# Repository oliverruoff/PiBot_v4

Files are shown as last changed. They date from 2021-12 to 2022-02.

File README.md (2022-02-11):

# PiBot_v4
A small roboter based on a raspberry pi zero w, using lidar for locating.

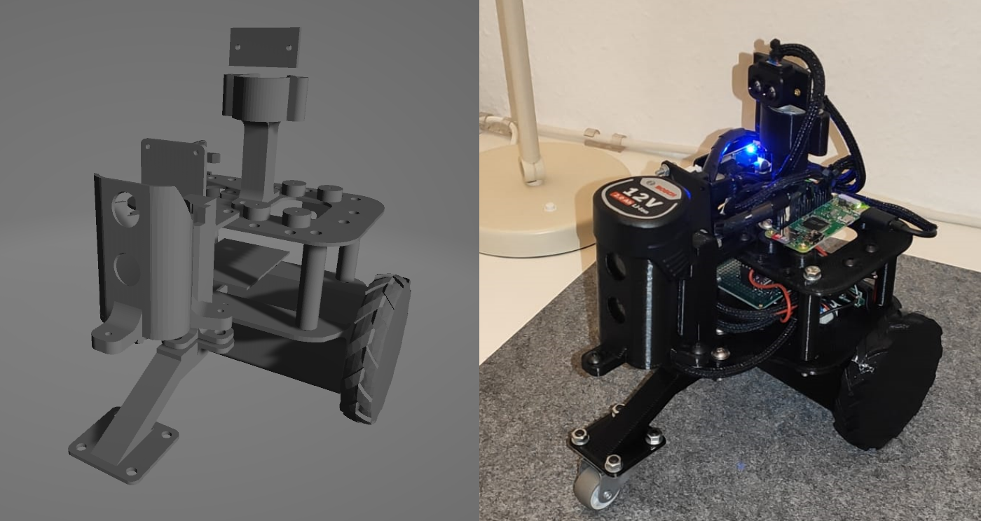
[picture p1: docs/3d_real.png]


## Results

First single mapping with single 360 scan:  
  
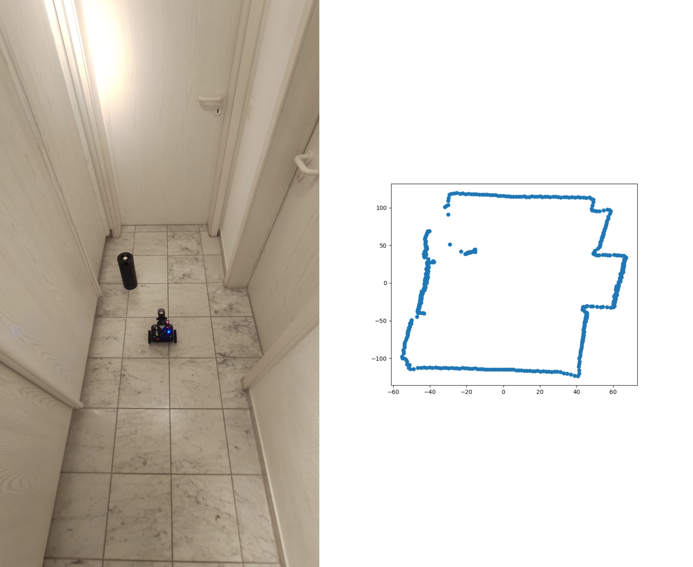
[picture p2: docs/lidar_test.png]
lidar test
  
  
"Manual" mapping results of six double 360 scans stitched together  
(ground truth map grey in the background):    

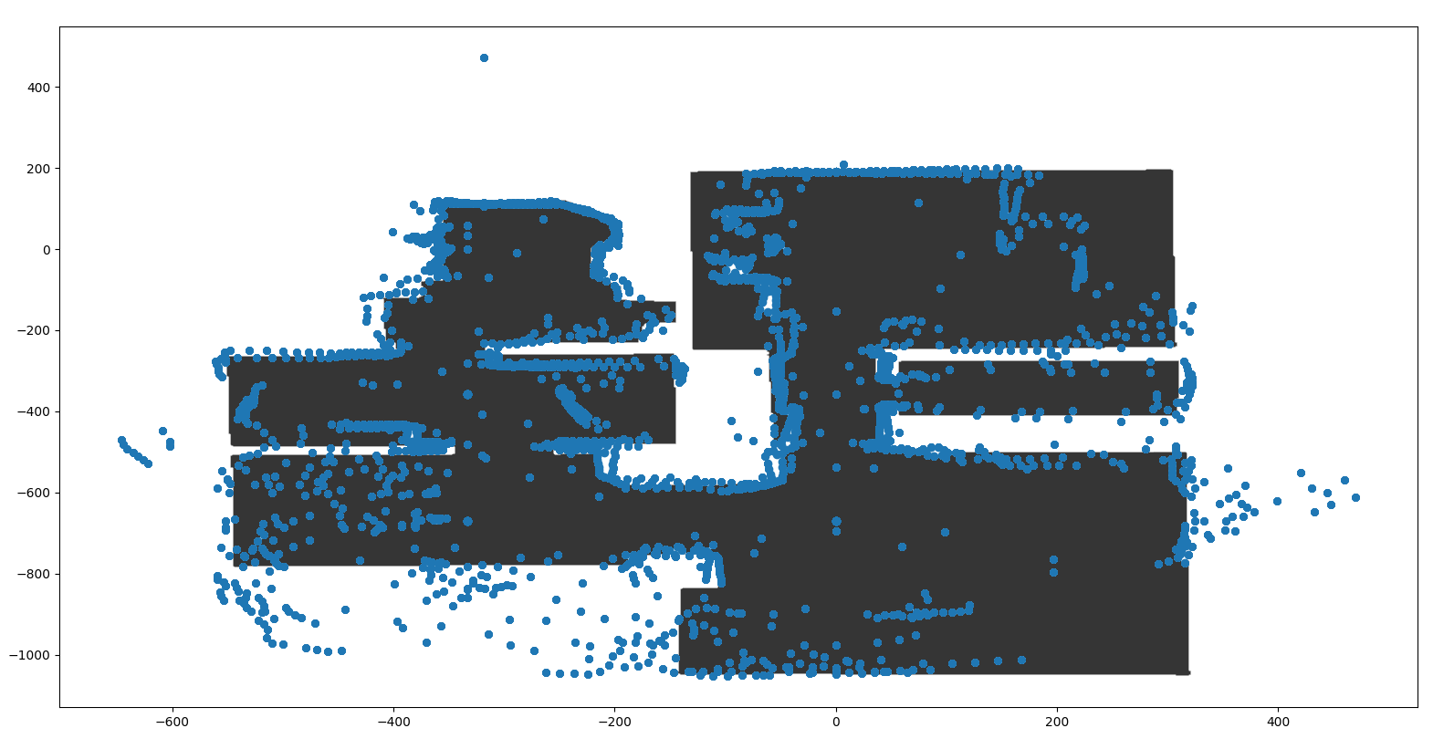
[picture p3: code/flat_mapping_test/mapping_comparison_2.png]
mapping comparison


## Setup

- Install python packages from requirements.txt
- Start pigpio demon on boot
    - `sudo systemctl enable pigpiod`
    - `sudo systemctl start pigpiod`
- Enable serial mode P6 in interacing options (`sudo raspi-config`)

## Printable 3D objects
The robot is designed by myself, the printable 3d objects can be found in the [stls folder](stls/).

## Wiring

Also see [fritzing wiring](docs/PiBot_v4_wiring.fzz).

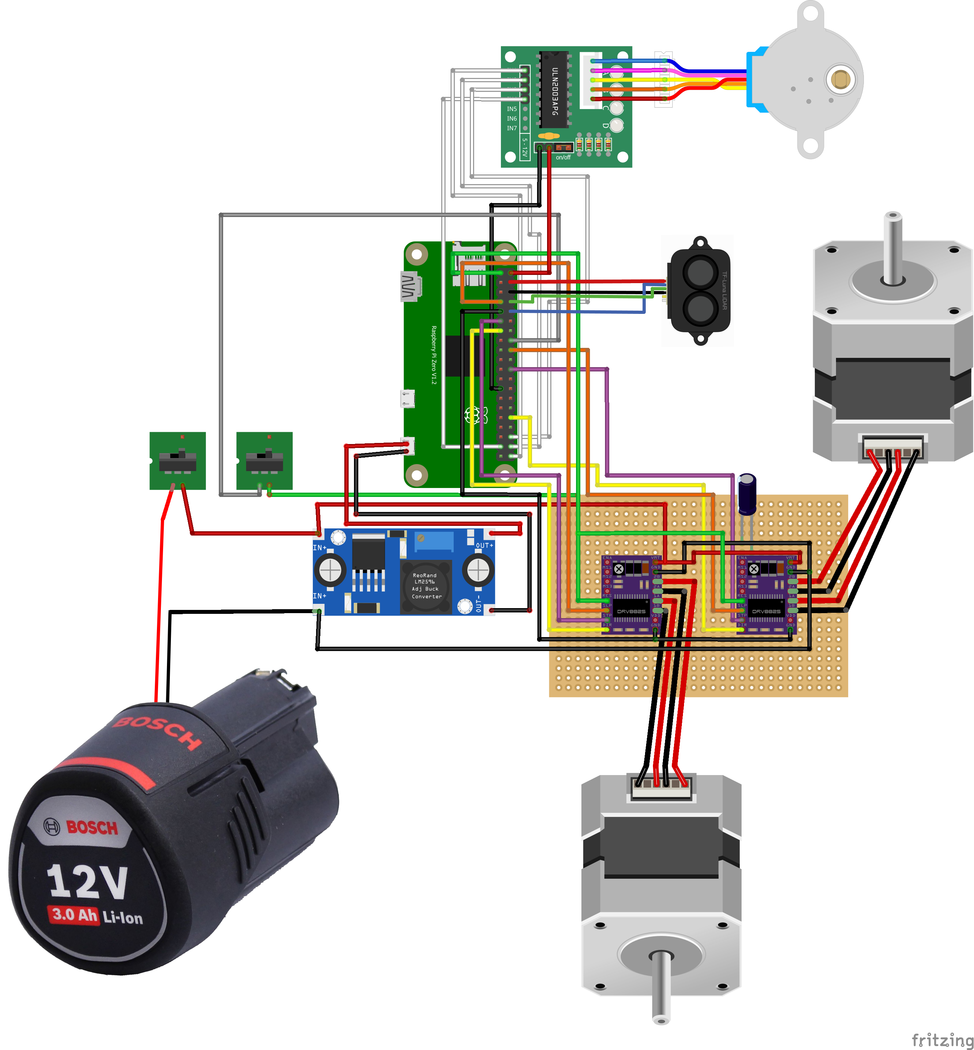
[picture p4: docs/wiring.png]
Breadboard View


## Stepper

To connect the stepper motor to the driver and raspberry, refer to this [youtube video](https://www.youtube.com/watch?v=LUbhPKBL_IU&t=258s).  
Don't miss to adjust the motor driver, so you don't fry your motor. (set current to max. 71% of max. motor current, in this case 1.5A --> driver current max. 1.065A (0.71 x 1.5). You should be fine with around 0.7A). --> For the smaller stepper which moves the lidar on the top, I used 0.5A, since this stepper has an 1A rating.

### Stepper ramping

The robot will slip when accelerating from 0 to 100% speed instantly, so that's why I implemented a ramping function (can be called by setting `ramping` keyword to true in according stepper functions).

The ramping function uses following exponential function:

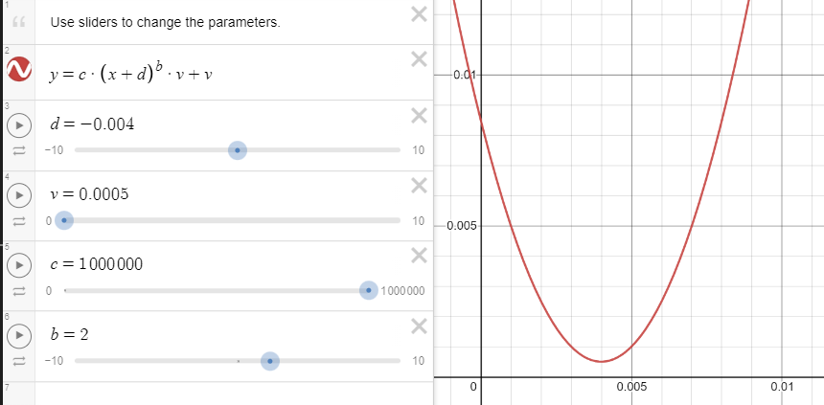
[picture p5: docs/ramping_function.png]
expo function

(using desmos.com) for modeling the function.

## Hardware Used

- Raspberry Pi Zero W
- Stepper Motor + Driver (DRV8825) ( 12V 1.5A) x2
- Stepper Motor + Driver ( 5V ULN2003)
- Power Converter
- TF Luna mini Lidar
- Bosch 12v Battery Pack
- Switches x2
- Voltage meter

### DRV8825 wiring

In order to correctly wire the bigger stepper motors, also see this example wiring:

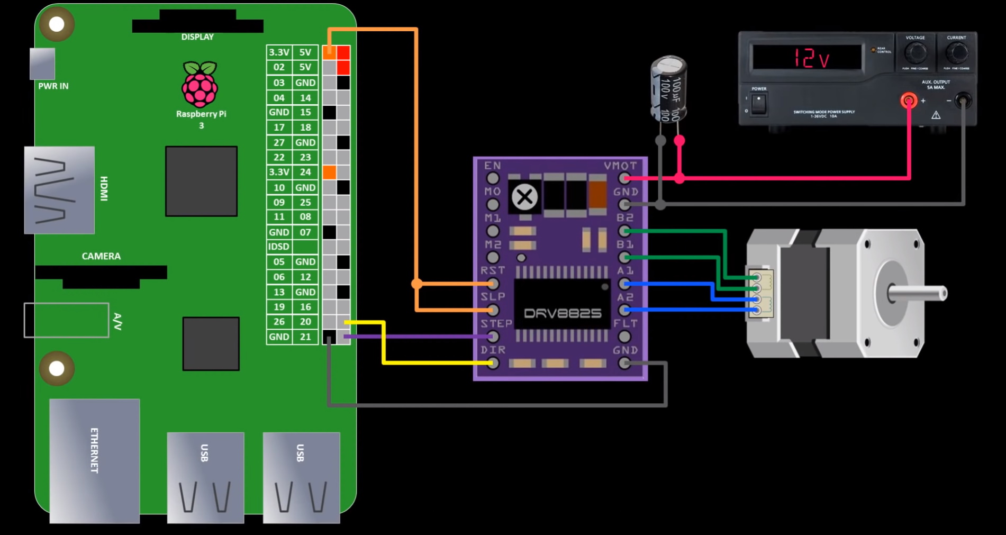
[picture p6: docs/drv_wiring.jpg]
drv wiring


### TF-Luna 

Check the byte codes of the lidar sensor for implementation:
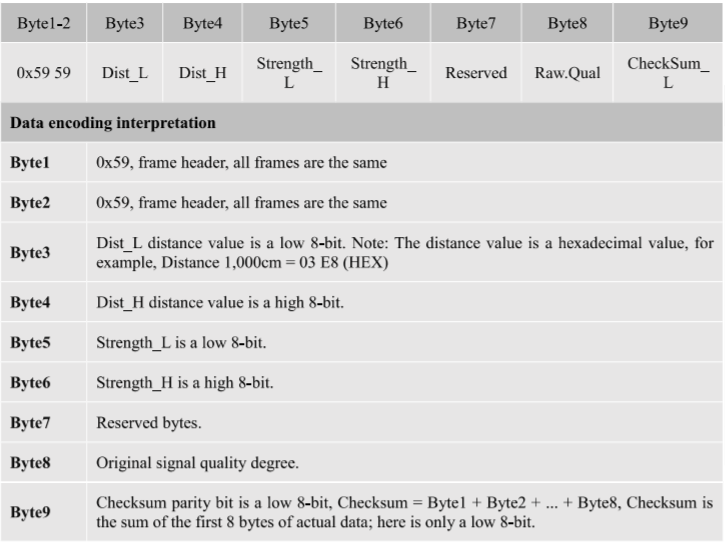
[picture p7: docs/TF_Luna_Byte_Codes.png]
tf-luna byte codes


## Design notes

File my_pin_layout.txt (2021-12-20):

Switch:

GPIO 23

Stepper rechts:

SLP = GPIO 24
STEP = GPIO 25
DIR= GPIO 12

Stepper links:

SLP = GPIO 4
STEP = GPIO 17
DIR = GPIO 27

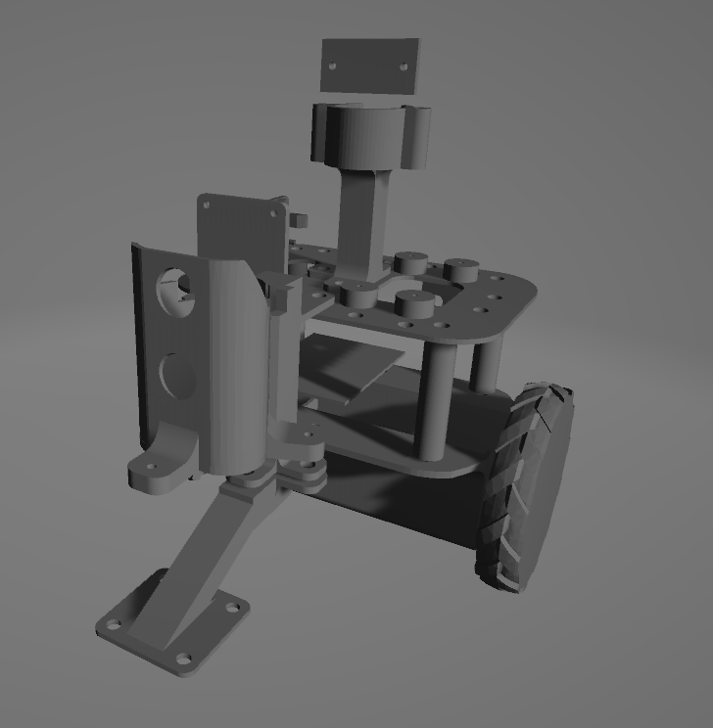
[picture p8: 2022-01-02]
docs/3d_robot.png

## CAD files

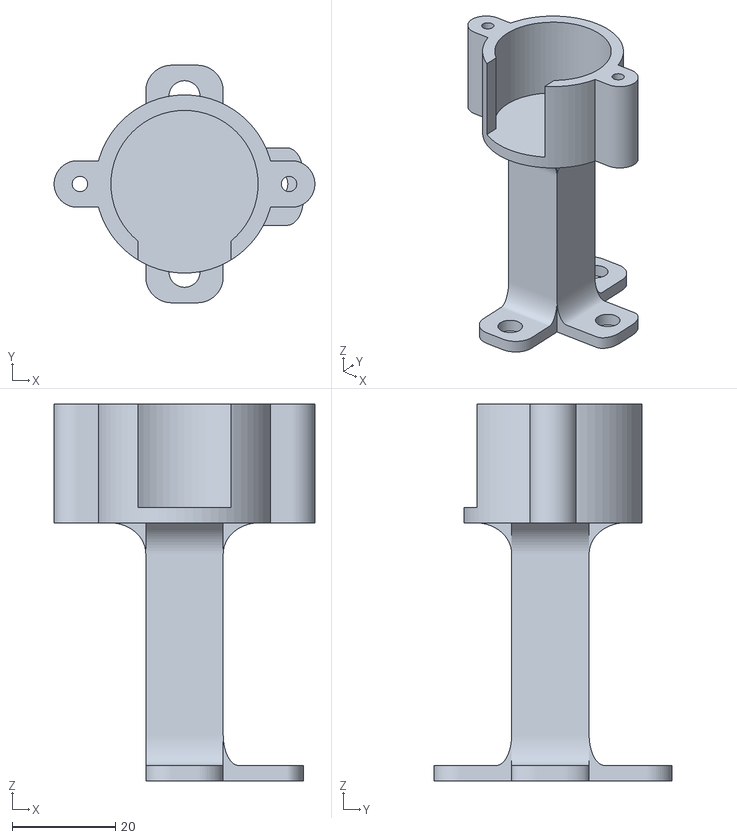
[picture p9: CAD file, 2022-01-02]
stls/PiBot v4_top_stepper_holder.stl
50.5 x 46.0 x 73.0

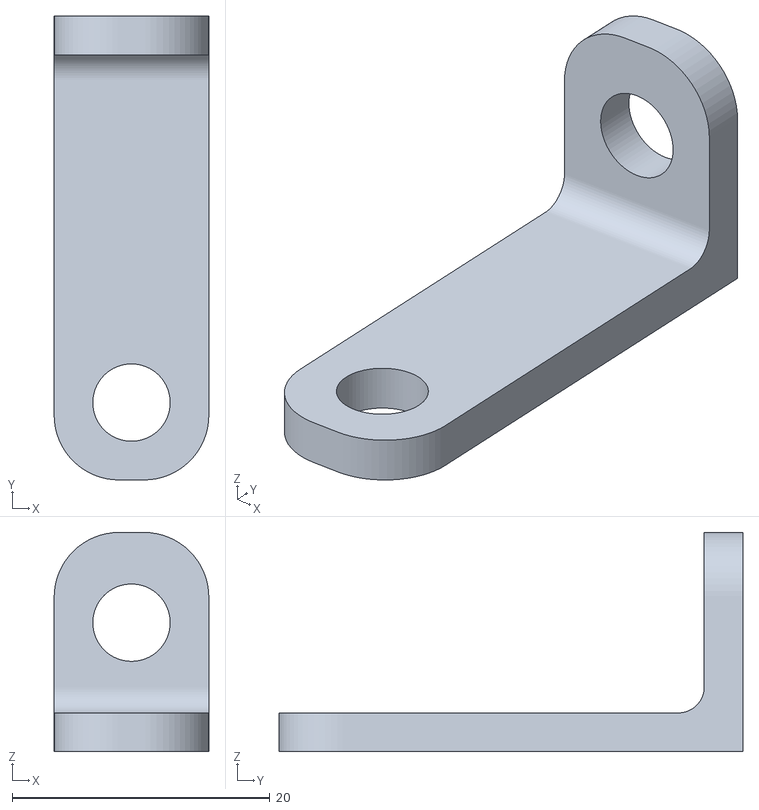
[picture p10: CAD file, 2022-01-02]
stls/PiBot v4_battery_holder_connector.stl
12.0 x 36.0 x 17.0

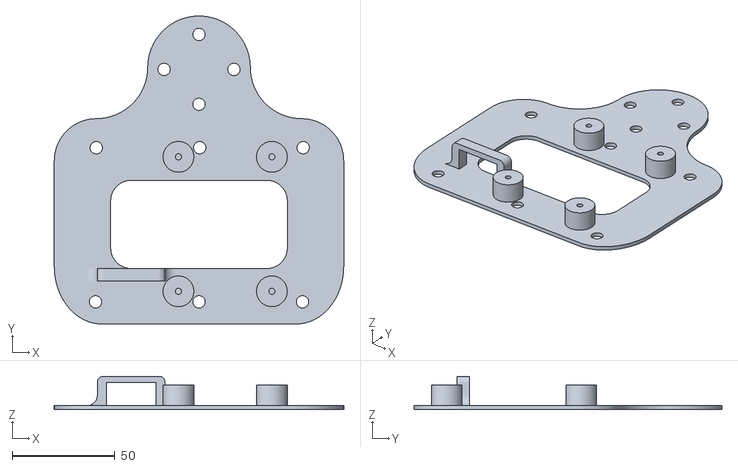
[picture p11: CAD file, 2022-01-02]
stls/PiBot v4_first_level_plate.stl
141.0 x 150.0 x 16.3

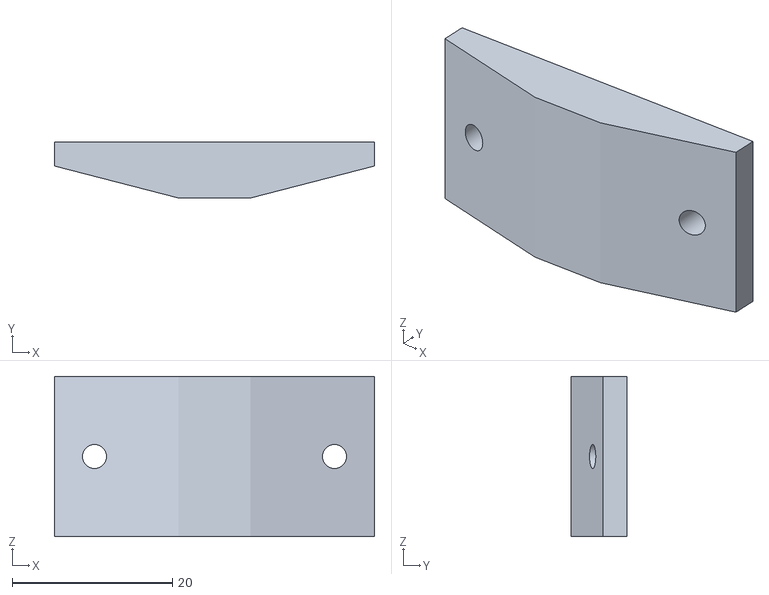
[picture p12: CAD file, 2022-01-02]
stls/PiBot v4_tf_luna_holder.stl
40.0 x 7.00 x 20.0

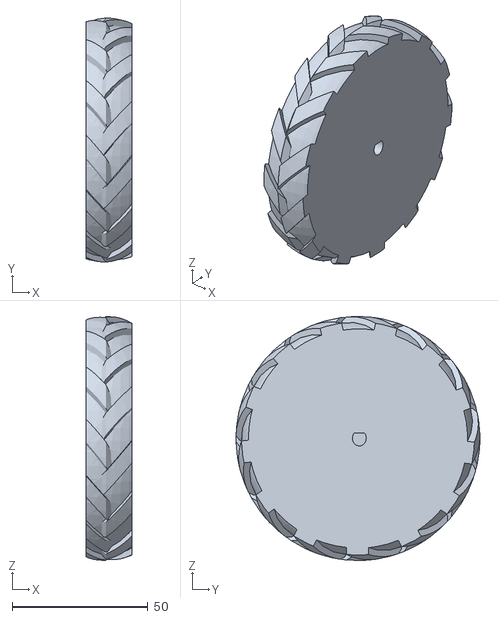
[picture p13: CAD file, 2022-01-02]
stls/PiBot v4_wheel.stl
17.0 x 90.0 x 90.0

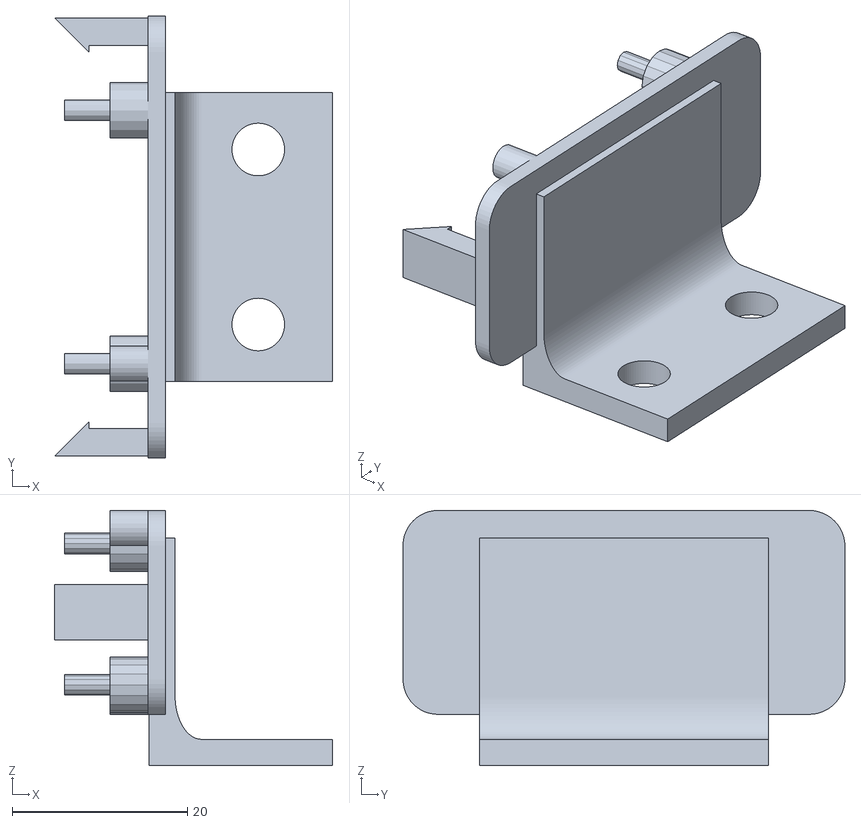
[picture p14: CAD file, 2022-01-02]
stls/PiBot v4_power_converter_holder.stl
31.8 x 50.5 x 29.1

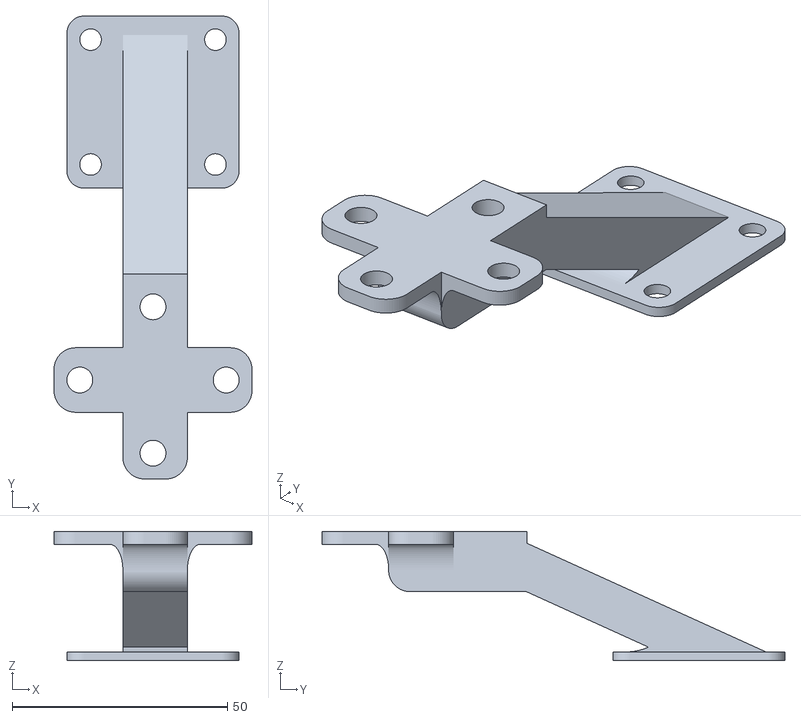
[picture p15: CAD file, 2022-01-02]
stls/PiBot v4_front_wheel_holder.stl
46.0 x 107.6 x 30.0

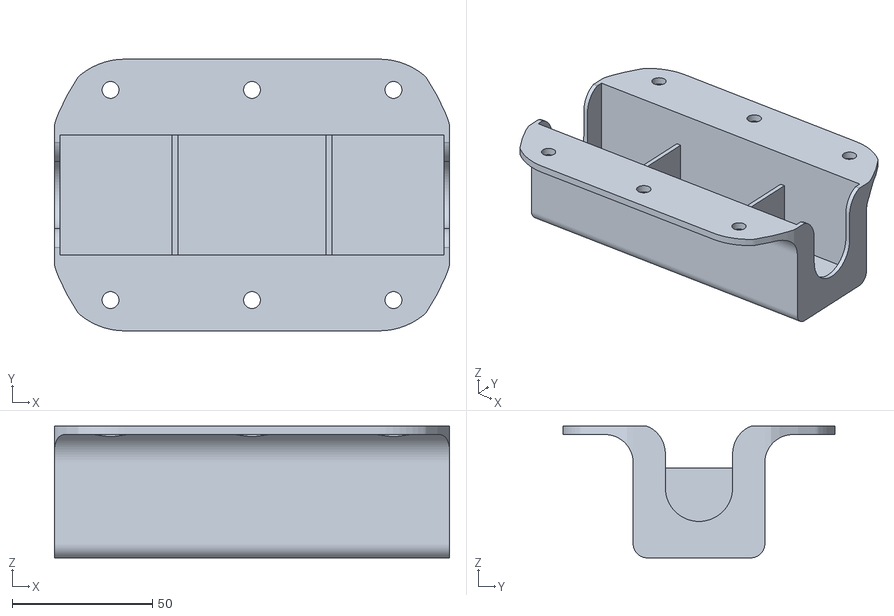
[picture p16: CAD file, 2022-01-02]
stls/PiBot v4_base_stepper_plate.stl
141.0 x 97.0 x 47.0

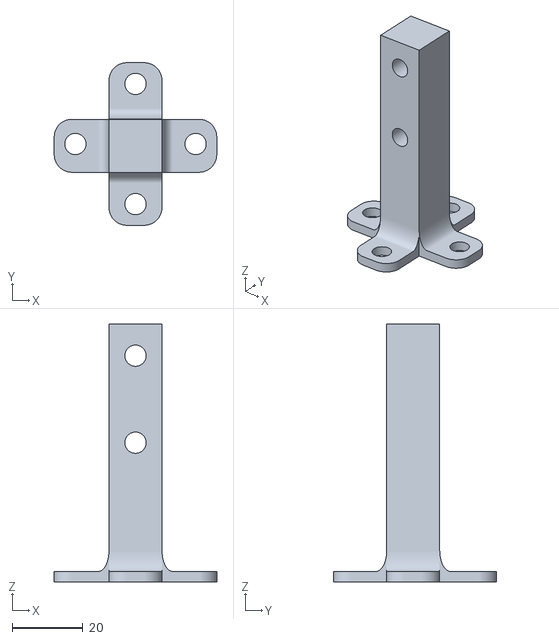
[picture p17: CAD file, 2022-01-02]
stls/PiBot v4_battery_holder.stl
46.0 x 46.0 x 73.0

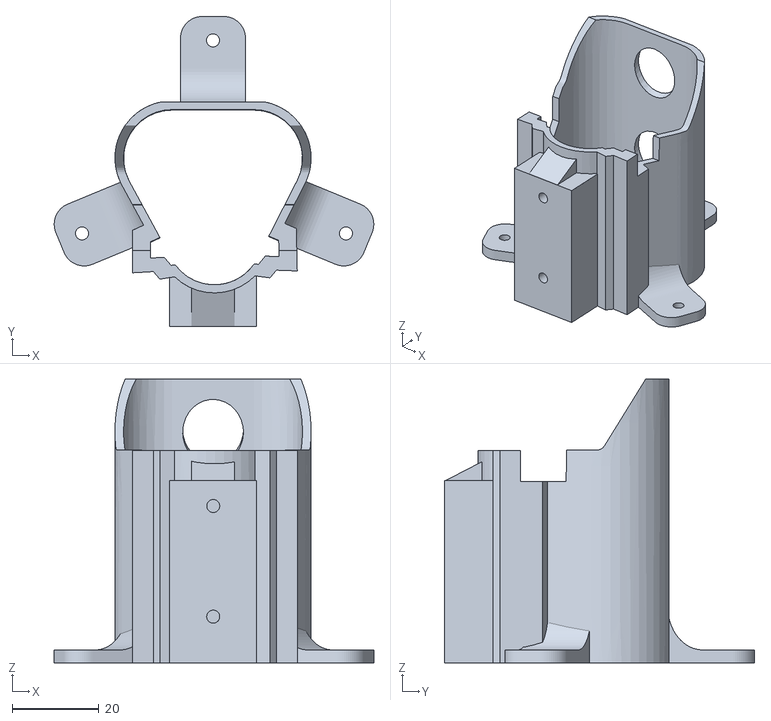
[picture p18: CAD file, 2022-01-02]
stls/PiBot v4_battery_case_top.stl
73.7 x 71.5 x 65.4

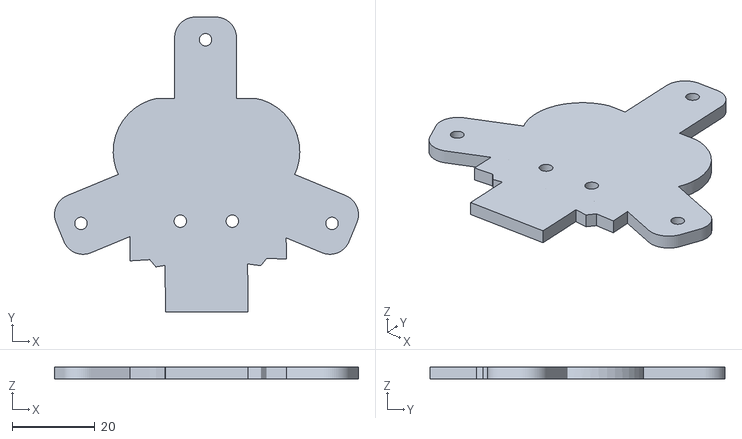
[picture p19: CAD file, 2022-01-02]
stls/PiBot v4_battery_case_bottom.stl
73.7 x 71.5 x 3.00

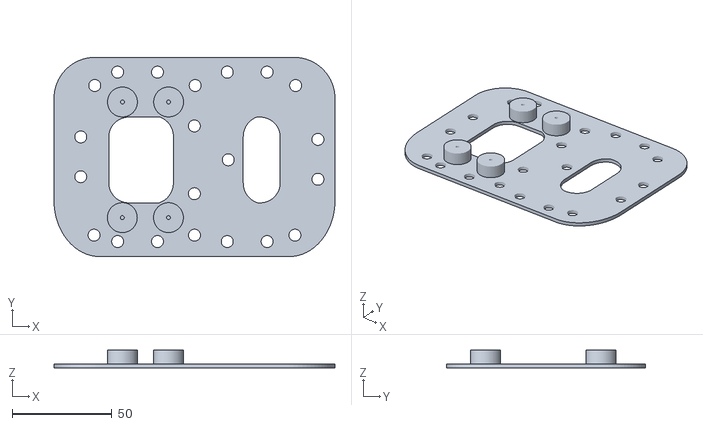
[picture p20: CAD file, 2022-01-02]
stls/PiBot v4_second_level_plate.stl
141.0 x 100.0 x 9.00

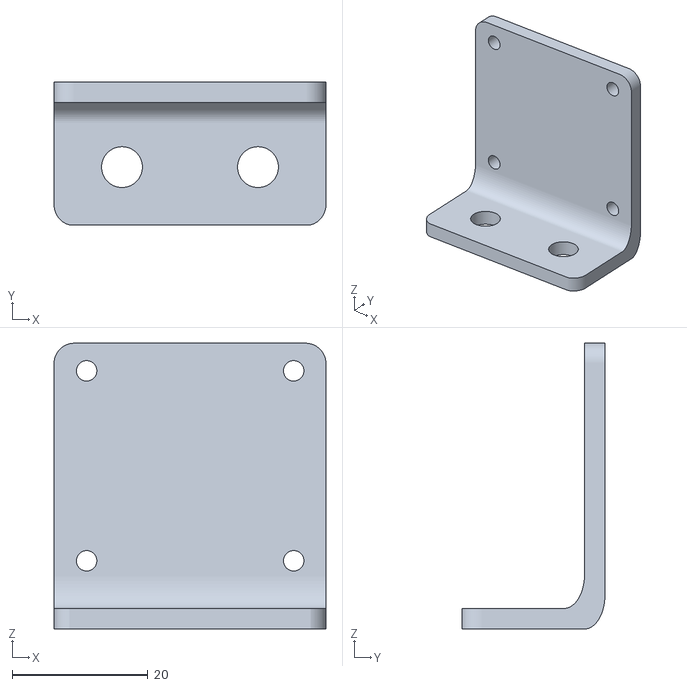
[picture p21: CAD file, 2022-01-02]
stls/PiBot v4_ULN2003_stepper_driver_holder.stl
40.0 x 21.0 x 42.0

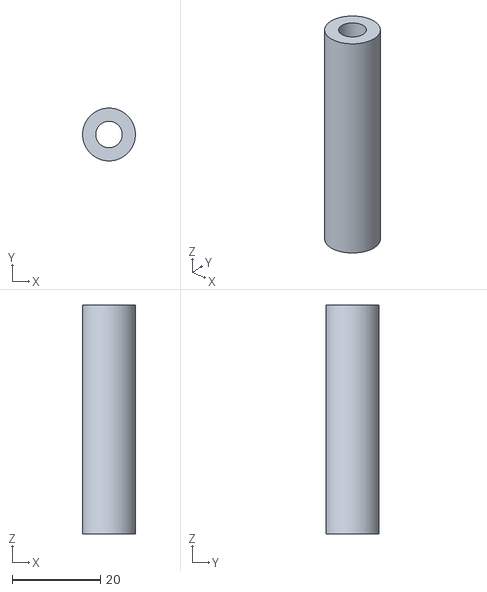
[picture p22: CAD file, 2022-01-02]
stls/PiBot v4_connectors.stl
12.0 x 12.0 x 52.0

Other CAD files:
stls/PiBot v4_switch_holder.stl

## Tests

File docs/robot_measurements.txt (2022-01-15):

Dro = 21,2cm
Uro = 66,6cm
Dre = 9,2
Ure = 28,9

Eine Umdrehung:
66,6 / 28,9 == 2,3
2,3 * 360° == 828°

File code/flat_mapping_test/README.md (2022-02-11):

# Flat Mapping Test

## Description

In this test I'm trying to map my flat by doing 360 scans with the robot on  
specified points.  
Therefore, I manually put the robot exactly to on the points and start a 360 scan  
by hand. The points are precisely measured and their offsets will be used to   
translate the resulting scanned coordinates.  
After postprocessing (translating) the scanned points and stitching them together,  hopefully a rough point cloud describing the flat should result.  

## Measurement points

>Note: The robot is facing the bottom of the map

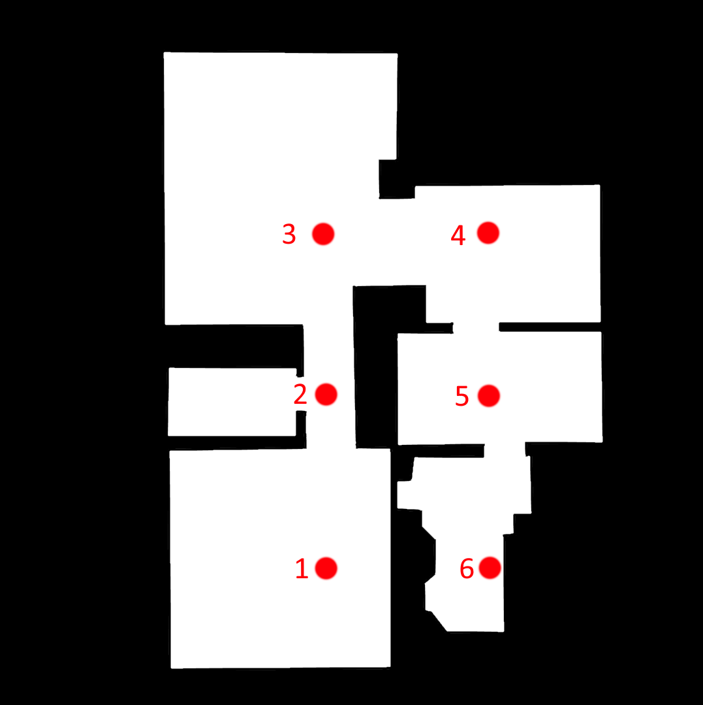
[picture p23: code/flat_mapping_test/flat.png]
flat with points


1.      (0, 0)  
1.      (0, -358)       // +0, -358
1.      (0, -671)       // +0, -313
1.      (-333, -671)    // -333, +0
1.      (-333, -358)    // +0, +313
1.      (-333, 0)       // +0, +358

## Results

Here the results of the approaches are listed.

### Manual movement approach

Comparison of the created point cloud map and the ground truth map:  
  
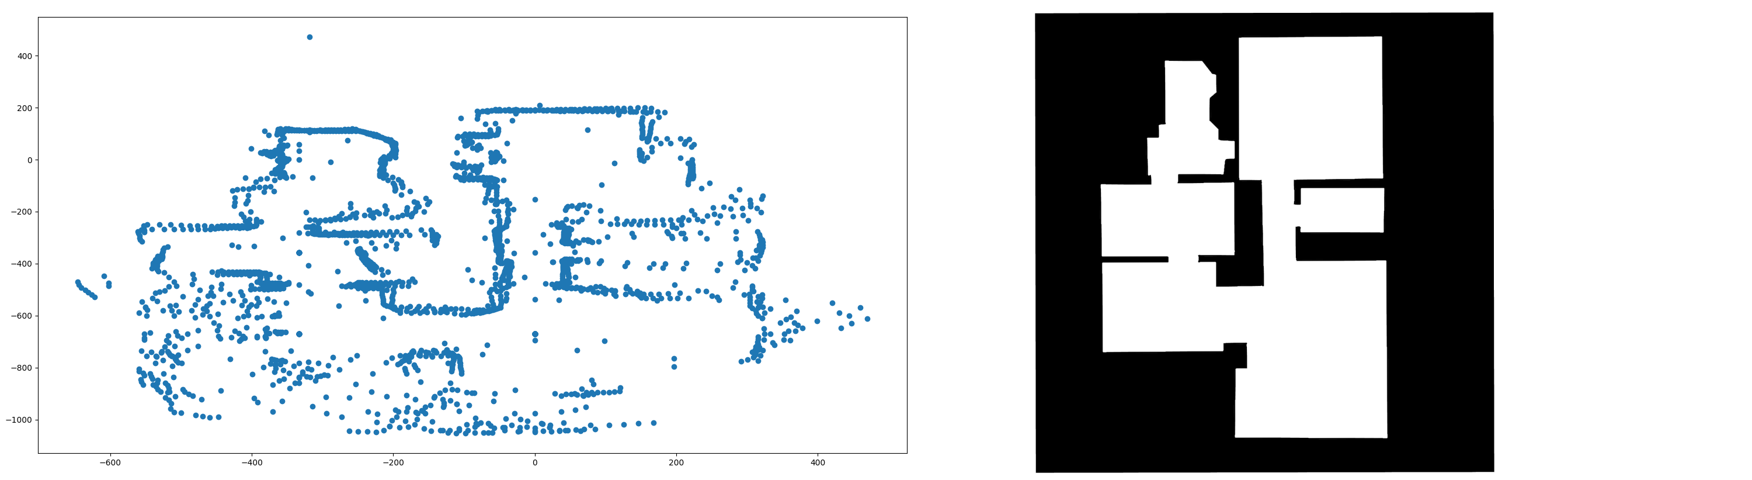
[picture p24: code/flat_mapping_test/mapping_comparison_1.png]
mapping comparison 1
  
  
Comparison of created point cloud map and ground truth map with scaling aligned:  
  
mapping comparison 2

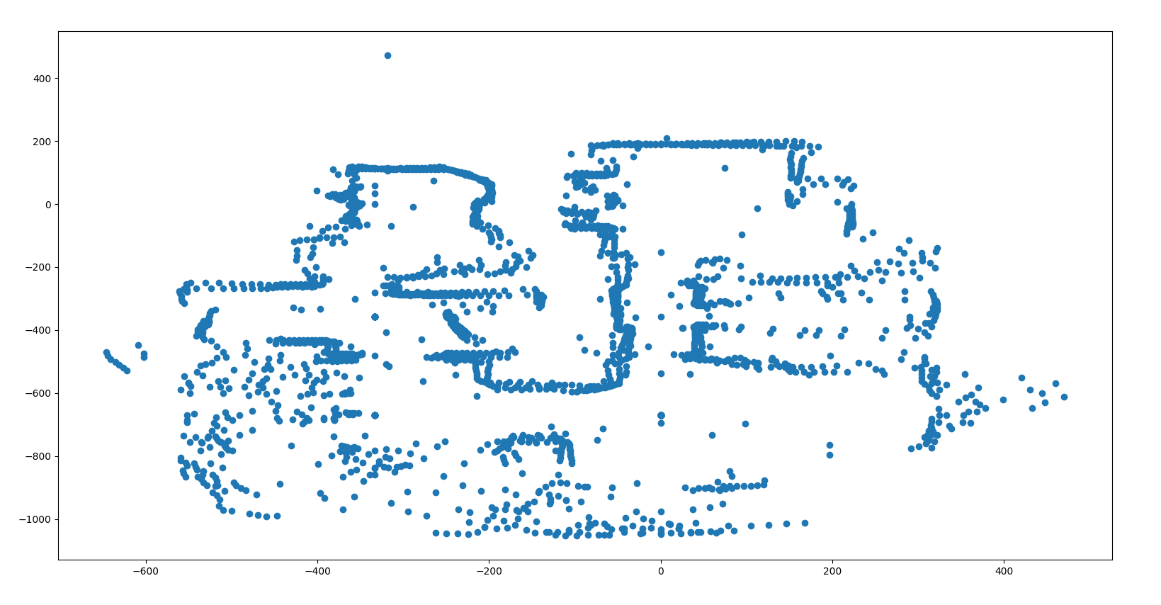
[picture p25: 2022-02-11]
code/flat_mapping_test/mapped_flat_first_attempt.png

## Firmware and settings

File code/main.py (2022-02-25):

from multiprocessing import Process

from actuators import stepper
from sensors import tfluna
from routines import test_all, recorder
from lidar import lidar
from combination import robot
from slam import slam

import RPi.GPIO as GPIO

####################################
# Initializing sensors, motors, etc.
####################################

left_stepper = stepper.stepper(
    DIR=27, STEP=17, SLP=4, steps_per_revolution=200, stepper_delay_seconds=0.0005, gpio_mode=GPIO.BCM)

right_stepper = stepper.stepper(
    DIR=12, STEP=25, SLP=24, steps_per_revolution=200, stepper_delay_seconds=0.0005, gpio_mode=GPIO.BCM)

top_stepper = stepper.stepper(
    DIR=6, STEP=26, SLP=13, RST=19, steps_per_revolution=200, stepper_delay_seconds=0.005, gpio_mode=GPIO.BCM)

tfluna = tfluna.TFLuna()
slam_ = slam.Slam()

robo = robot.Robot(left_stepper, right_stepper, top_stepper, tfluna)

while True:
    inp = input("Input: "). split(" ")
    a = inp[0]
    if a == "1":
        top_stepper.make_one_step()
    elif a == "2":
        # toggle top_stepper direction
        top_stepper.set_direction_clockwise(
            not top_stepper.is_direction_clockwise())
    elif a == "3":
        # drive top_stepper certain angle
        top_stepper.turn_stepper_angle(
            int(inp[1]), asynch=False, ramping=False)
    elif a == "4":
        # drive robot certain distance in cm
        robo.drive_cm(int(inp[1]), bool(inp[2]))
    elif a == "5":
        # turn robot certain angle in degree
        robo.turn_degree(int(inp[1]), bool(inp[2]))
    elif a == "6":
        recorder.record(left_stepper, right_stepper)
    elif a == "7":
        robo.start()
    elif a == "8":
        print(tfluna.read_tfluna_data())
    elif a == "9":
        top_stepper.deactivate_stepper()
        left_stepper.deactivate_stepper()
        right_stepper.deactivate_stepper()
    elif a == "10":
        cloud_1 = robo.lidar.scan_angle_with_stepper_position_reset(360)
        robo.drive_cm(50, forward=True)
        cloud_2 = robo.lidar.scan_angle_with_stepper_position_reset(360)
        moved_cloud = slam_.find_cloud_translation_and_rotation(cloud_1, cloud_2)[
            :-1]
        print(moved_cloud)
        print(moved_cloud[-1])
    elif a == "11":
        cloud_1 = robo.lidar.scan_angle_with_stepper_position_reset(360)
        cloud_2 = slam_.rotate_cloud(cloud_1, 90)
        print("____________________________________")
        print([(i[0], i[1]) for i in cloud_1])
        print("____________________________________")
        print(cloud_2)
    elif a == "12":
        cloud_1 = robo.lidar.scan_angle_with_stepper_position_reset(360)
        robo.drive_cm(50, forward=True)
        cloud_2 = robo.lidar.scan_angle_with_stepper_position_reset(360)
        cloud_3 = slam_.translate_cloud(cloud_2, 0, 50)
        print('Score 1:', slam_.score_2d_clouds(cloud_1, cloud_2))
        print('Score 2:', slam_.score_2d_clouds(cloud_1, cloud_3))
        print("____________________________________")
        print([(i[0], i[1]) for i in cloud_1])
        print("____________________________________")
        print([(i[0], i[1]) for i in cloud_2])
        print("____________________________________")
        print(cloud_3)
    else:
        print("Command not recognized!")

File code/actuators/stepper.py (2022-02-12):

from time import sleep
import threading

import RPi.GPIO as GPIO
import pigpio

CW = 1     # Clockwise Rotation
CCW = 0    # Counterclockwise Rotation


class stepper:
    """This class is for handling the DRV8825 motor driver. E.g. to operate
        common bigger stepper motors.
        """

    def __init__(self, DIR, STEP, SLP, steps_per_revolution, RST=None, stepper_delay_seconds=.005, gpio_mode=GPIO.BCM):
        self.DIR = DIR
        self.STEP = STEP
        self.RST = RST
        # If set to Low, there is no holding torque on the motor
        self.SLP = SLP
        # Steps per Revolution (360 / 1.8) (1,8° per step (oruoff))
        self.steps_per_revolution = steps_per_revolution

        self.stepper_delay_seconds = stepper_delay_seconds
        self.gpio_mode = gpio_mode

        self.pi = pigpio.pi()

        self.direction = CW

        GPIO.setmode(gpio_mode)

        if RST is not None:
            GPIO.setup(self.RST, GPIO.OUT)
            GPIO.output(self.RST, GPIO.HIGH)

        GPIO.setup(self.DIR, GPIO.OUT)
        GPIO.setup(self.STEP, GPIO.OUT)
        GPIO.setup(self.SLP, GPIO.OUT)

        GPIO.output(DIR, CW)

    def set_stepper_delay(self, stepper_delay_seconds):
        """Sets the delay in seconds for the driver to wait between steps.

        Args:
            stepper_delay_seconds (float): Delay in seconds to wait between steps.
        """
        self.stepper_delay_seconds = stepper_delay_seconds

    def activate_stepper(self):
        """Activates the stepper, which also will put holding torque on the stepper.
        This is required in order to move the stepper.
        """
        GPIO.output(self.SLP, GPIO.HIGH)

    def deactivate_stepper(self):
        """Deactivates the stepper and also releases holding torque on the stepper.
        In a deactivated state, the stepper will not be able to move.
        """
        GPIO.output(self.SLP, GPIO.LOW)

    def run_continuously(self, dutycycle=128, frequency=320):
        """Activated, the stepper will continuously run with the desired frequency.
        The dutycycle describes the distribution of high low states, where 128 is 50% / 50% high / low.

        Args:
            dutycycle (int, optional): Describes high / low ratio. 128 is 50%/50%. Defaults to 128.
            frequency (int, optional): Describes the frequency of the stepper's high / low states. Defaults to 320.
        """
        self.activate_stepper()
        self.pi.set_PWM_dutycycle(self.STEP, dutycycle)
        self.pi.set_PWM_frequency(self.STEP, frequency)

    def stop_continuous(self):
        """Stops the continuous turning of the stepper. Also deactivates it, thus
        releasing holding torque.
        """
        self.deactivate_stepper()
        self.pi.set_PWM_dutycycle(self.STEP, 0)

    def set_direction_clockwise(self, clockwise=True):
        """Sets the spinning direction of the stepper motor to clockwise or
        counterclockwise.

        Args:
            clockwise (bool, optional): Spinning direction. Defaults to True.
        """
        self.direction = CW if clockwise else CCW
        GPIO.output(self.DIR, self.direction)

    def is_direction_clockwise(self):
        """Returns True if the current direction set is clockwise, else False.

        Returns:
            bool: True if clockwise, else False.
        """
        return bool(self.direction)

    def turn_stepper_angle(self, degree, asynch, ramping=False):
        """Turns the stepper for a precise angle. Can be called
        either synchronous or asynchronously.

        Args:
            degree (int): The angle in degree, on how much the stepper will
            rotate.
            asynch (bool): Flag wheather this function (and therefore the motor), will turn
            synchronously or asynchronously.
        """
        if (asynch):
            thread = threading.Thread(
                target=self._turn_stepper, args=([degree, ramping]), kwargs={})
            thread.start()
        else:
            self._turn_stepper(degree, ramping)

    def _ramping_function(self, current_step, all_steps):
        """Uses a defined exponential function to output the y value, which can be used
        as delay for the stepper

        Args:
            current_step (int): The current step number (iteratively increased)
            all_steps (int): The number of all steps for the current movement.

        Returns:
            float: The resulting y value, which can be used as stepper delay in seconds.
        """
        X_AXIS_SHIFT = -0.004
        GRAPH_WIDTH = abs(2*X_AXIS_SHIFT)
        EXPONENT = 2
        PARABOLA_SHARPNESS = 1000000
        x = GRAPH_WIDTH/all_steps*current_step
        y = PARABOLA_SHARPNESS*pow(x+X_AXIS_SHIFT, EXPONENT) * \
            self.stepper_delay_seconds + self.stepper_delay_seconds
        return y

    def _turn_stepper(self, degree, ramping=False):
        """This function is for turning the stepper for a precise angle.
        This function should be called with the `turn_stepper_angle` function,
        defining whether the function should run synchronously or asynchronously.

        Args:
            degree (int): The angle in degree, on how much the stepper will rotate.
            ramping (bool): Defines wheather the stepper should ramp up and down its movement.
        """
        self.activate_stepper()
        steps = int(self.steps_per_revolution/360*degree)
        for i in range(steps):
            if ramping:
                delay = self._ramping_function(i, steps)
            else:
                delay = self.stepper_delay_seconds
            GPIO.output(self.STEP, GPIO.HIGH)
            sleep(delay)
            GPIO.output(self.STEP, GPIO.LOW)
            sleep(delay)

    def make_one_step(self):
        """Makes exactly one full step.
        """
        self.activate_stepper()
        GPIO.output(self.STEP, GPIO.HIGH)
        sleep(self.stepper_delay_seconds)
        GPIO.output(self.STEP, GPIO.LOW)
        sleep(self.stepper_delay_seconds)

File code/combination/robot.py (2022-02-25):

from lidar import lidar
import time


class Robot:

    def __init__(self, left_stepper, right_stepper, top_stepper, tfluna):
        self.left_stepper = left_stepper
        self.right_stepper = right_stepper
        self.top_stepper = top_stepper
        self.tfluna = tfluna

        self.position_X = 0
        self.position_Y = 0
        self.heading = 0

        self.TYRE_CIRCUMFERENCE_CM = 28.9              # manually determined
        self.ROBOT_CIRCUMFERENCE_CM = 60.3             # manually determined
        self.TURNING_ERROR_MULTIPLIER = 1.083          # manually determined

        self.lidar = lidar.Lidar(top_stepper=top_stepper, tfluna=tfluna)

    def drive_cm(self, cm, forward, ramping=True):
        if not forward:
            self.left_stepper.set_direction_clockwise(False)
            self.right_stepper.set_direction_clockwise(True)
        else:
            self.left_stepper.set_direction_clockwise(True)
            self.right_stepper.set_direction_clockwise(False)
        desired_angle = (cm / self.TYRE_CIRCUMFERENCE_CM) * \
            360 * self.TURNING_ERROR_MULTIPLIER
        self.left_stepper.turn_stepper_angle(
            desired_angle, True, ramping)
        self.right_stepper.turn_stepper_angle(
            desired_angle, False, ramping)

    def turn_degree(self, degree, clockwise, ramping=True):
        if clockwise:
            self.left_stepper.set_direction_clockwise(False)
            self.right_stepper.set_direction_clockwise(False)
        else:
            self.left_stepper.set_direction_clockwise(True)
            self.right_stepper.set_direction_clockwise(True)

        desired_angle = (self.ROBOT_CIRCUMFERENCE_CM /
                         self.TYRE_CIRCUMFERENCE_CM) * degree * self.TURNING_ERROR_MULTIPLIER
        self.left_stepper.turn_stepper_angle(
            desired_angle, True, ramping)
        self.right_stepper.turn_stepper_angle(
            desired_angle, False, ramping)
        self.heading = (self.heading +
                        degree) % 360 if clockwise else (self.heading - degree) % -360

    def max_distance_routine(self):
        while True:
            env = lidar.scan_360(self.top_stepper, self.tfluna)
            max_dist = 0
            max_angle = 0
            for i in env:
                if i[2] > 800:
                    continue
                if i[2] > max_dist:
                    max_dist = i[2]
                    max_angle = i[3]
            dist_cm = max_dist
            # dist_cm = self.tfluna.read_distance() * 100
            print("Dist:", dist_cm, "at angle:", max_angle)
            if dist_cm > 40:
                self.turn_degree(max_angle, True)
                self.drive_cm(int(dist_cm/1.1), True)
            else:
                self.drive_cm(20, False)
                self.turn_degree(120, True)

    def start(self):
        self.top_stepper.activate_stepper()
        while True:
            env_map = self.lidar.scan_angle_to_left_and_right(degree=45)
            distances = [i[2] for i in env_map if i[2] != 0]
            dist_cm = min(distances)
            print('MIN DISTANCE: ', dist_cm)
            distances = []
            if dist_cm > 40:
                self.drive_cm(cm=dist_cm-30, forward=True, ramping=True)
            else:
                self.turn_degree(degree=45, clockwise=True, ramping=True)
                print("My current heading:", self.heading)

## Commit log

2021-12-20 test left stepper
2021-12-20 add DRV8825 class for better stepper driver usage
2021-12-20 added PWM functionality
2021-12-20 combined stepper activation in PWM logic
2021-12-20 added stepper activation
2021-12-20 removed stepper deactivation bug
    [DRV8825.py]
2021-12-20 decreased stepper frequency
2021-12-25 Added top stepper control
2021-12-25 added tf luna sensor
2022-01-02 Added some documentation (wiring etc.)
    [PiBot_v4_wiring.fzz]
2022-01-02 Added stls
    [PiBot v4_ULN2003_stepper_driver_holder.stl, PiBot v4_base_stepper_plate.stl, PiBot v4_battery_case_bottom.stl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]
2022-01-02 added lidar scanning 360
2022-01-02 changed 360° lidar movement
2022-01-02 added first lidar test
2022-01-15 fix DRV8825 stepper delay
    [DRV8825.py]
2022-01-15 stepper tests
2022-01-15 changed stepper delay
2022-01-15 increased stepper delay
2022-01-15 again increased stepper delay
2022-01-15 changed stepper delays
2022-01-15 activated holding torque on passive stepper
2022-01-15 lidar test
2022-01-16 added stepper async movement
2022-01-16 added async stepper movement
2022-01-16 fix async function call
    [DRV8825.py]
2022-01-16 fix user input colliding with variable
    [recorder.py]
2022-01-16 add hol´ding torque
2022-01-16 removed wait for thread option
2022-01-16 added ramp up for steppers
2022-01-16 increased min stepper delay
2022-01-16 fixed ramp down only
    [DRV8825.py]
2022-01-17 added forth and back lidar scan
2022-01-17 fix lidar angle ccw calculation
    [lidar.py]
2022-01-17 changed lidar scan360 to one time
2022-01-17 switched distance calc to cm
2022-01-17 now only approach until <40cm
2022-01-17 switched to continuous stepper mode
2022-01-17 slowed stepper
2022-01-17 slowed down stepper even more
2022-01-21 changed top stepper
2022-01-21 changed stepper sequence
2022-01-21 switched lidar code to new stepper motor
2022-01-21 worked on lidar logic
2022-01-21 reset stepper position after lidar 360 scan
    [lidar.py]
2022-01-31 changed top stepper to DRV8825
2022-01-31 added one step fnc to DRV8825 driver
2022-01-31 top stepper test
2022-02-06 testing top stepper
2022-02-06 testing stepper #2
2022-02-08 removed stepper de/activation from make_step fnc
2022-02-08 checking lidar
2022-02-08 removed halfstep from lidar
2022-02-08 rename stepper class & removed deact. stepper after turning
2022-02-08 stepper 360 test
2022-02-08 removed ramp phases for lidar scanning
2022-02-08 fix lidar 360 scan
    [lidar.py]
2022-02-08 lidar fixed
2022-02-09 implemented expo. fnc for ramping steppers
2022-02-09 fix old ramp fnc for comparison
    [stepper.py]
2022-02-10 activating stepper within make_one_step fnc
2022-02-12 switched robo front
2022-02-12 increased motor speed
2022-02-12 added error multiplier in turning
    [robot.py]
2022-02-12 added error also in movement
    [robot.py]
2022-02-12 changed stepper speed
2022-02-12 activating top stepper for fix lidar
    [robot.py]
2022-02-12 added 0 distance error fix
    [robot.py]
2022-02-12 complete lidar change to OO
2022-02-12 casted steps to int in case degree calc isn't precisely a step number
2022-02-12 Refactored lidar
2022-02-12 added lidar calibration
2022-02-13 calibrated lidar calibration
2022-02-13 added more logic to calibration
2022-02-13 increased calibration distance
2022-02-13 added stepper deactivation to main routine
2022-02-13 starting server from main thread
2022-02-13 starting server again from main thread
2022-02-13 starting flask in main thread
2022-02-13 changed lidar calibrarion behavior
2022-02-13 ignoring 0 at lidar calibration
2022-02-13 changed lidar calib. offset
2022-02-13 changed offset of lidar calibration
2022-02-13 switching back to old driving logic
2022-02-25 removed lidar calibration
2022-02-25 switched translation direction
